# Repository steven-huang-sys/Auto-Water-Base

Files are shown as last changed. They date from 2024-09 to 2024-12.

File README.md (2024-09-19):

# Senior Design Project Fall 2024
## Autonomous Watering System - Base Station
This repository contains the code for the microcontroller used in the base station of the system. Not everything is uploaded as the repository would be way too big with the build files. I used the ESP-IDF setup within VSCode.

## Specifications
### Microcontrollers
Tested on an ESP-WROOM-32
Intended to be an ESP32-S3 on the final product

### Display
2.2in TFT LCD Display with ILI9488 Drivers. SPI interface

## Schematic Notes
This is on KiCAD 6.0. Footprints for the ESP32 can be found here: https://github.com/espressif/kicad-libraries/tree/legacy_kicad6?tab=readme-ov-file

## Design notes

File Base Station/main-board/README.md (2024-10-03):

# Main Board of the Base Station
This contains the code and build for the ESP32 planned to be inside the hub.

## Self Notes
- Remember to run the menuconfig as Bluetooth needs to be enabled before the code can be built. Adding an sdkconfig.default would also work.
- Currently using NimBLE instead of Bluedroid stack as we likely don't need Bluetooth Classic.

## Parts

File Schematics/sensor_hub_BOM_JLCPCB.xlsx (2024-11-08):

Comment | Designator | Footprint | JLCPCB Part#(optional)
1u | C1, C6, C18 | Capacitor_SMD:C_0805_2012Metric_Pad1.18x1.45mm_HandSolder | C116352
4.7u | C2 | Capacitor_SMD:C_0805_2012Metric_Pad1.18x1.45mm_HandSolder | C1779
10u | C3, C19 | Capacitor_SMD:C_0805_2012Metric_Pad1.18x1.45mm_HandSolder | C15850
0.1u | C4, C5, C8, C9, C12 | Capacitor_SMD:C_0805_2012Metric_Pad1.18x1.45mm_HandSolder | C1711
15p | C7, C10 | Capacitor_SMD:C_0805_2012Metric_Pad1.18x1.45mm_HandSolder | C63339
22u | C11 | Capacitor_SMD:C_0805_2012Metric_Pad1.18x1.45mm_HandSolder | C45783
1n | C13, C14, C15, C16, C17 | Capacitor_SMD:C_0805_2012Metric_Pad1.18x1.45mm_HandSolder | C46653
ESD9B5.0ST5G | D1, D2, D8 | Diode_SMD:D_SOD-923 | C111566
LED | D3, D4, D6, D7 | LED_SMD:LED_0805_2012Metric_Pad1.15x1.40mm_HandSolder | C2297
40V | D5 | Diode_SMD:D_SOD-123F | C779674
120 ohms | FB1 | Resistor_SMD:R_0805_2012Metric_Pad1.20x1.40mm_HandSolder | C79382
MountingHole | H1, H2, H3, H4, H5, H6 | MountingHole:MountingHole_3.2mm_M3
USB_C_Receptacle_USB2.0 | J1 | Connector_USB:USB_C_Receptacle_HRO_TYPE-C-31-M-12 | C165948
Conn_01x03 | J2 | Connector_JST:JST_PH_B3B-PH-K_1x03_P2.00mm_Vertical | C131339
Conn_01x09_Male | J3 | Connector_PinHeader_2.54mm:PinHeader_1x09_P2.54mm_Vertical | C22438292
BC818 | Q1, Q2 | Package_TO_SOT_SMD:SOT-23 | C154797
4.12k | R1 | Resistor_SMD:R_0805_2012Metric_Pad1.20x1.40mm_HandSolder | C218607
1.18k | R2 | Resistor_SMD:R_0805_2012Metric_Pad1.20x1.40mm_HandSolder | C2077400
1.13k | R3 | Resistor_SMD:R_0805_2012Metric_Pad1.20x1.40mm_HandSolder | C322246
5.1k | R4, R5 | Resistor_SMD:R_0805_2012Metric_Pad1.20x1.40mm_HandSolder | C26023
1.5k | R6, R7, R8 | Resistor_SMD:R_0805_2012Metric_Pad1.20x1.40mm_HandSolder | C126687
300 | R9 | Resistor_SMD:R_0805_2012Metric_Pad1.20x1.40mm_HandSolder | C2828726
R | R10, R13 | Resistor_SMD:R_0805_2012Metric_Pad1.20x1.40mm_HandSolder | C25275
Optional | R11 | Resistor_SMD:R_0805_2012Metric_Pad1.20x1.40mm_HandSolder
10k | R12, R15, R16, R17, R18, R19, R20, R21, R22, R23, R24, R28, R31, R32 | Resistor_SMD:R_0805_2012Metric_Pad1.20x1.40mm_HandSolder | C17414
0 | R14, R29, R30, R33, R34 | Resistor_SMD:R_0805_2012Metric_Pad1.20x1.40mm_HandSolder | C25275
22.1k | R25 | Resistor_SMD:R_0805_2012Metric_Pad1.20x1.40mm_HandSolder | C17552
47.5k | R26 | Resistor_SMD:R_0805_2012Metric_Pad1.20x1.40mm_HandSolder | C26011
1k | R27 | Resistor_SMD:R_0805_2012Metric_Pad1.20x1.40mm_HandSolder | C25623
SW_Push | SW1, SW2 | JLCPCB_Components:Switch_Small | C967766
SW_Push | SW3, SW4, SW5, SW6, SW7 | Button_Switch_THT:SW_PUSH-12mm
BQ24074RGT | U1 | Package_DFN_QFN:VQFN-16-1EP_3x3mm_P0.5mm_EP1.6x1.6mm | C54313
LD1117S33TR_SOT223 | U2 | Package_TO_SOT_SMD:SOT-223-3_TabPin2 | C86781
ESP32-S3-WROOM-1 | U3 | Espressif:ESP32-S3-WROOM-1U | C3013946
CP2102N-Axx-xQFN28 | U4 | Package_DFN_QFN:QFN-28-1EP_5x5mm_P0.5mm_EP3.35x3.35mm | C964632
32.768 kHz | Y1 | Crystal:Crystal_SMD_3215-2Pin_3.2x1.5mm

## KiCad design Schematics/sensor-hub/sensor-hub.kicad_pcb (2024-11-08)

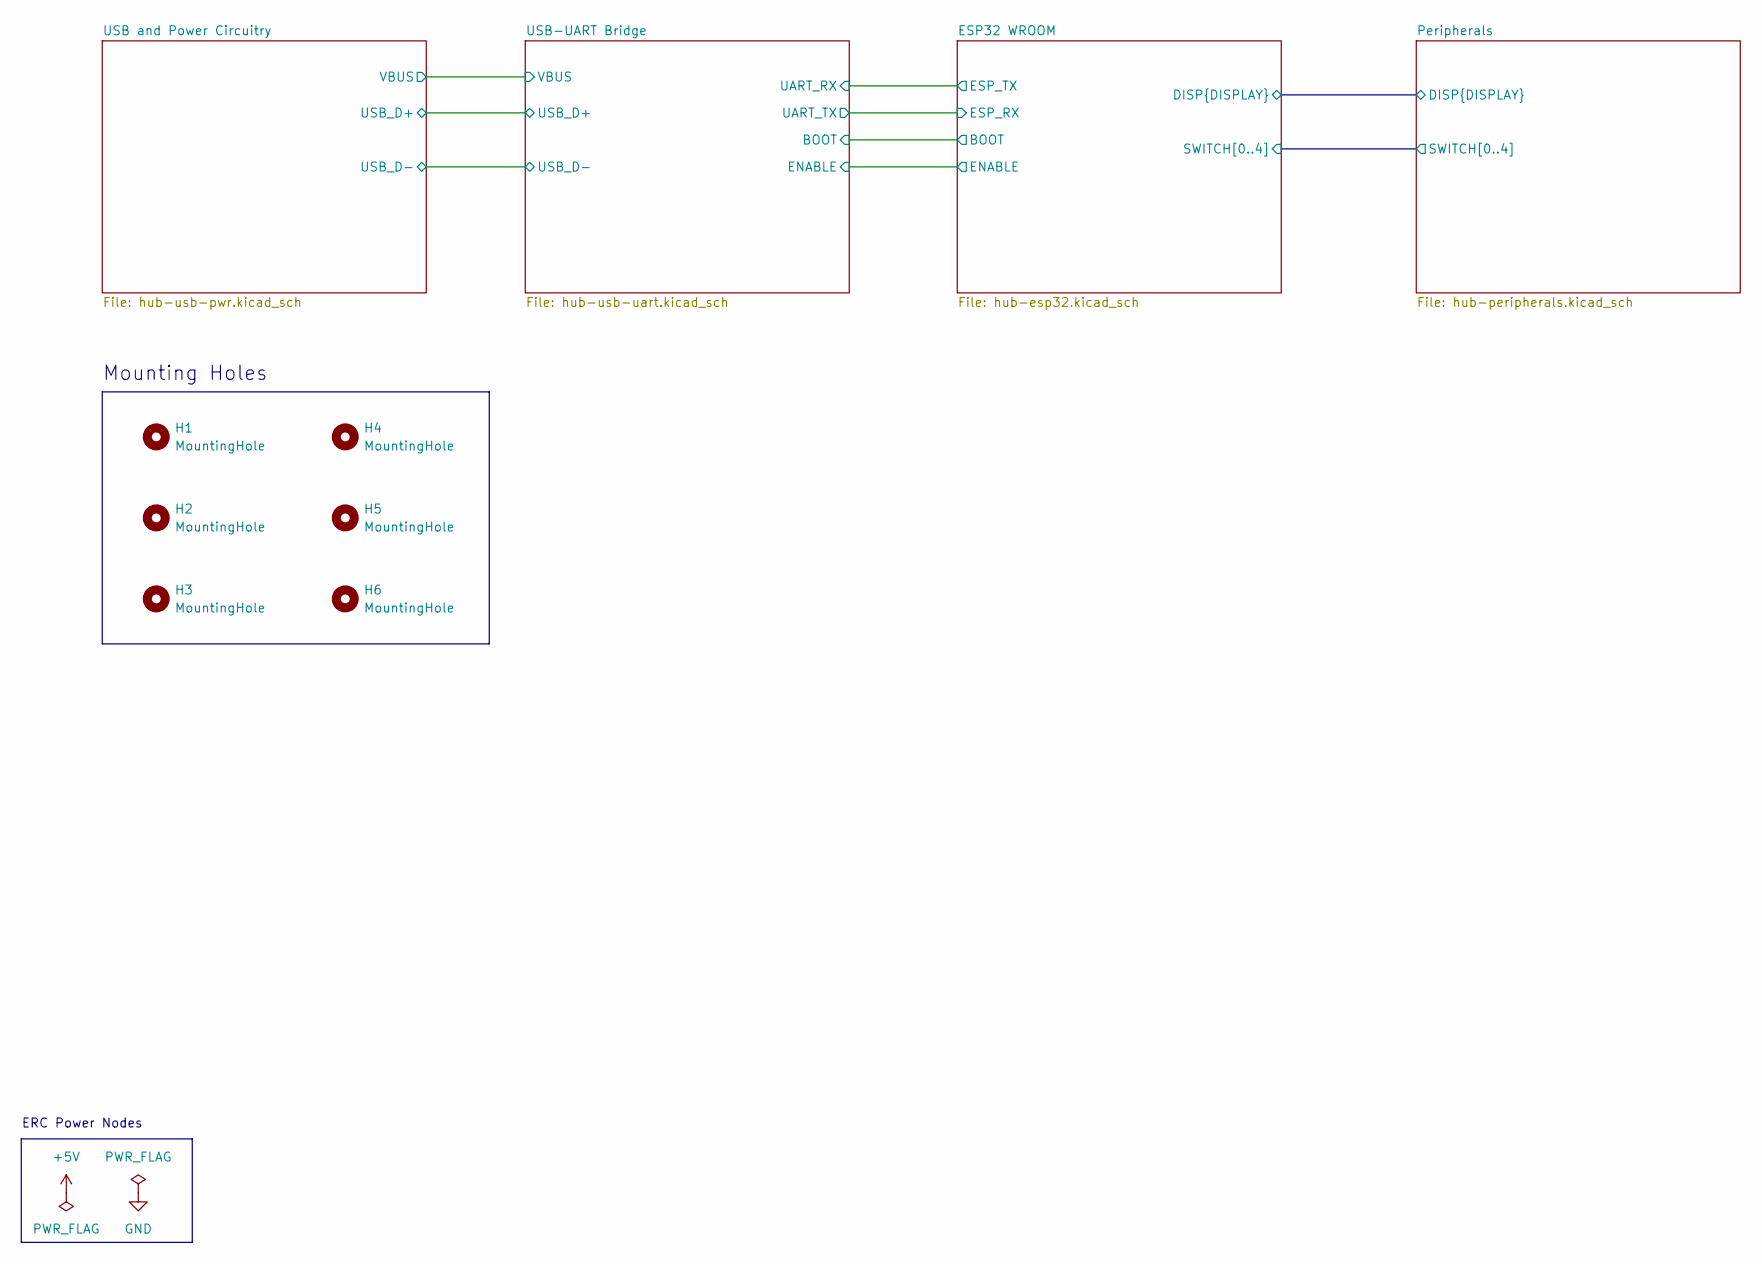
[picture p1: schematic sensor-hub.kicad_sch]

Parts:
H1, H2, H3, H4, H5, H6: MountingHole; MountingHole_3.2mm_M3

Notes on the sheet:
ERC Power Nodes
Mounting Holes

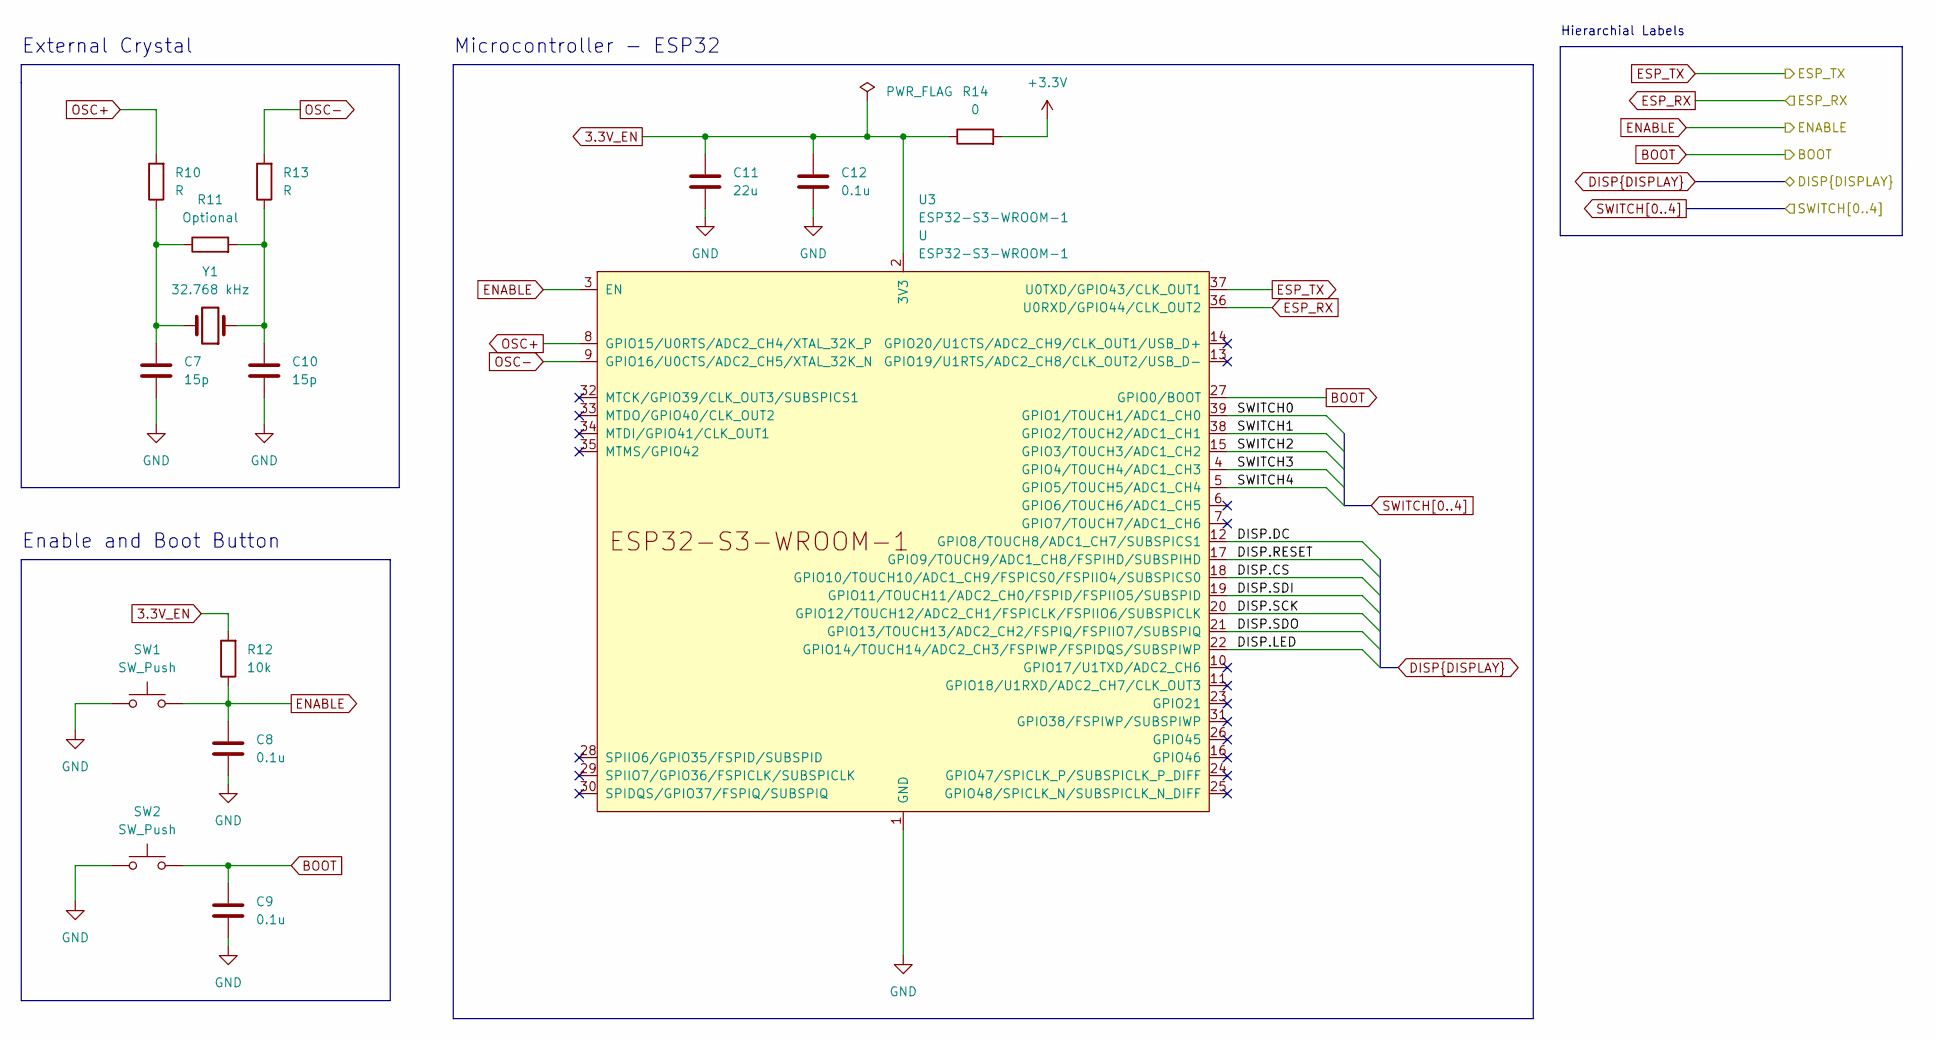
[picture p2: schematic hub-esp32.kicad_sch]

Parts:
C7, C10: 15p; C_0805_2012Metric_Pad1.18x1.45mm_HandSolder
C8, C9, C12: 0.1u; C_0805_2012Metric_Pad1.18x1.45mm_HandSolder
C11: 22u; C_0805_2012Metric_Pad1.18x1.45mm_HandSolder
R10, R13: R; R_0805_2012Metric_Pad1.20x1.40mm_HandSolder
R11: Optional; R_0805_2012Metric_Pad1.20x1.40mm_HandSolder
R12: 10k; R_0805_2012Metric_Pad1.20x1.40mm_HandSolder
R14: 0; R_0805_2012Metric_Pad1.20x1.40mm_HandSolder
SW1, SW2: SW_Push; Switch_Small
U3: ESP32-S3-WROOM-1; ESP32-S3-WROOM-1U
Y1: 32.768 kHz; Crystal_SMD_3215-2Pin_3.2x1.5mm

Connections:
3.3V_EN: C11.2, C12.2, R12.2, R14.1, U3.2 (3V3)
+3V3: R14.2; also elsewhere on the board
BOOT: C9.2, SW2.2, U3.27 (GPIO0/BOOT); also elsewhere on the board
DISP.CS: U3.18 (GPIO10/TOUCH10/ADC1_CH9/FSPICS0/FSPIIO4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); also elsewhere on the board
DISP.DC: U3.12 (GPIO8/TOUCH8/ADC1_CH7/SUBSPICS1); also elsewhere on the board
DISP.LED: U3.22 (GPIO14/TOUCH14/ADC2_CH3/FSPIWP/FSPIDQS/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); also elsewhere on the board
DISP.RESET: U3.17 (GPIO9/TOUCH9/ADC1_CH8/FSPIHD/SUBSPIHD); also elsewhere on the board
DISP.SCK: U3.20 (GPIO12/TOUCH12/ADC2_CH1/FSPICLK/FSPIIO6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); also elsewhere on the board
DISP.SDI: U3.19 (GPIO11/TOUCH11/ADC2_CH0/FSPID/FSPIIO5/S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); also elsewhere on the board
DISP.SDO: U3.21 (GPIO13/TOUCH13/ADC2_CH2/FSPIQ/FSPIIO7/S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); also elsewhere on the board
ENABLE: C8.2, R12.1, SW1.2, U3.3 (EN); also elsewhere on the board
ESP_RX: U3.36 (U0RXD/GPIO44/CLK_OUT2); also elsewhere on the board
GND: C7.2, C8.1, C9.1, C10.2, C11.1, C12.1, SW1.1, SW2.1, U3.1 (GND), U3.40 (GND), U3.41 (GND); also elsewhere on the board
unnamed: C7.1, R10.1, R11.1, Y1.2
unnamed: C10.1, R11.2, R13.1, Y1.1
OSC+: R10.2, U3.8 (GPIO15/U0RTS/ADC2_CH4/XTAL_32K_P)
OSC-: R13.2, U3.9 (GPIO16/U0CTS/ADC2_CH5/XTAL_32K_N)
SWITCH0: U3.39 (GPIO1/TOUCH1/ADC1_CH0); also elsewhere on the board
SWITCH1: U3.38 (GPIO2/TOUCH2/ADC1_CH1); also elsewhere on the board
SWITCH2: U3.15 (GPIO3/TOUCH3/ADC1_CH2); also elsewhere on the board
SWITCH3: U3.4 (GPIO4/TOUCH4/ADC1_CH3); also elsewhere on the board
SWITCH4: U3.5 (GPIO5/TOUCH5/ADC1_CH4); also elsewhere on the board
UART_RX: U3.37 (U0TXD/GPIO43/CLK_OUT1); also elsewhere on the board

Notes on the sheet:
External Crystal
Enable and Boot Button
Hierarchial Labels
Microcontroller - ESP32

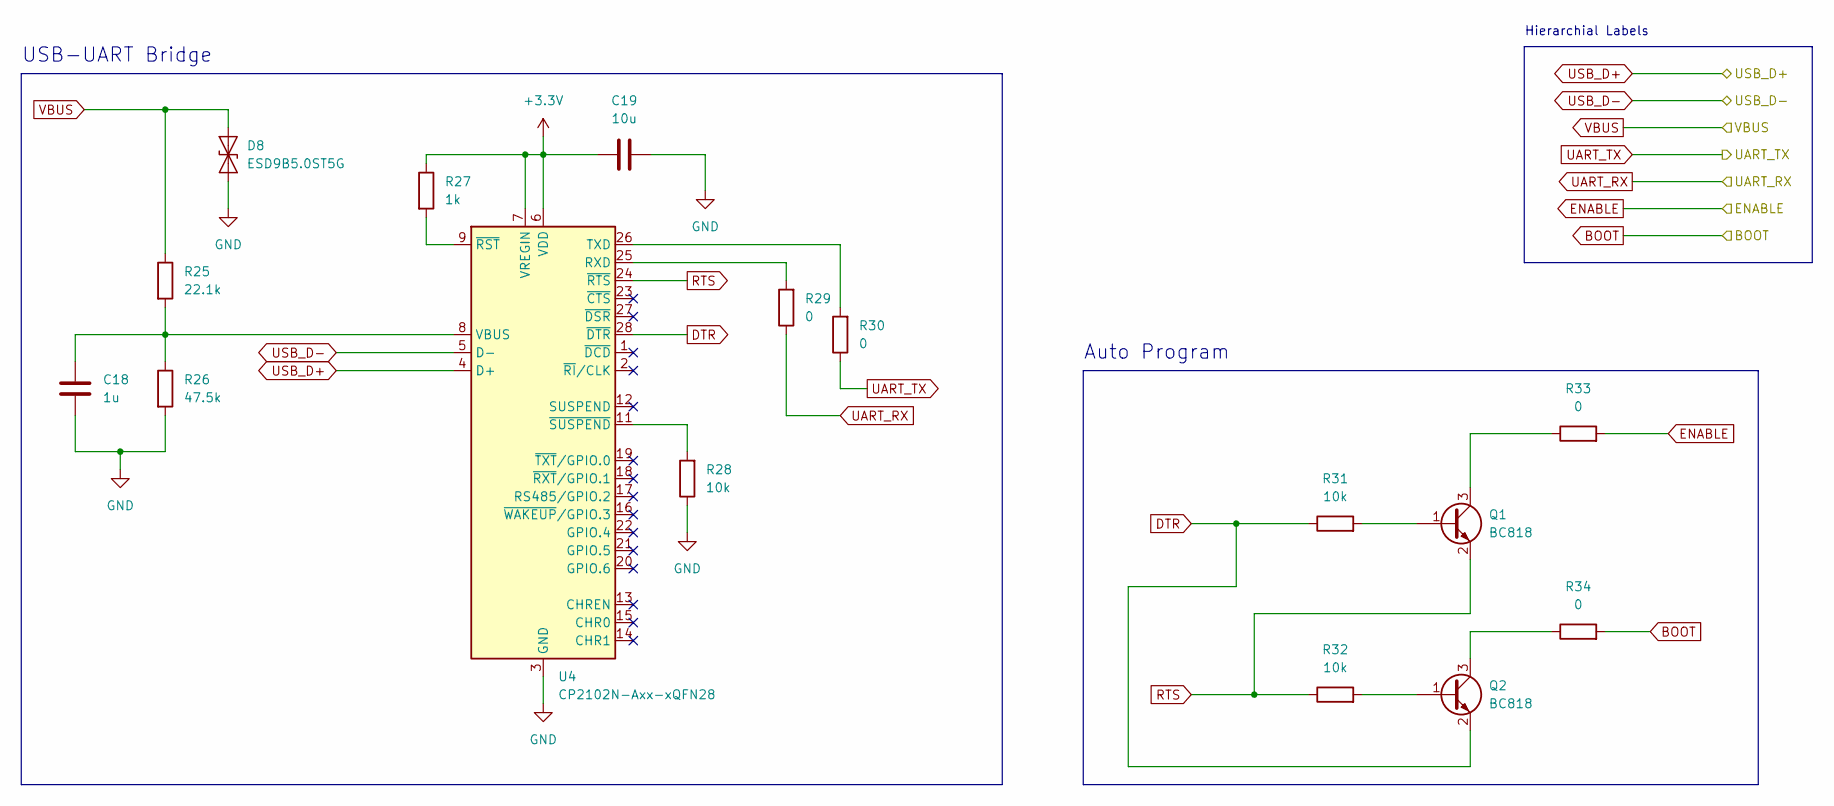
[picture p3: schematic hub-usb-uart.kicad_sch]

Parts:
C18: 1u; C_0805_2012Metric_Pad1.18x1.45mm_HandSolder
C19: 10u; C_0805_2012Metric_Pad1.18x1.45mm_HandSolder
D8: ESD9B5.0ST5G; D_SOD-923
Q1, Q2: BC818; SOT-23
R25: 22.1k; R_0805_2012Metric_Pad1.20x1.40mm_HandSolder
R26: 47.5k; R_0805_2012Metric_Pad1.20x1.40mm_HandSolder
R27: 1k; R_0805_2012Metric_Pad1.20x1.40mm_HandSolder
R28, R31, R32: 10k; R_0805_2012Metric_Pad1.20x1.40mm_HandSolder
R29, R30, R33, R34: 0; R_0805_2012Metric_Pad1.20x1.40mm_HandSolder
U4: CP2102N-Axx-xQFN28; QFN-28-1EP_5x5mm_P0.5mm_EP3.35x3.35mm

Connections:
+3V3: C19.1, R27.1, U4.6 (VDD), U4.7 (VREGIN); also elsewhere on the board
BOOT: R34.2; also elsewhere on the board
DTR: Q2.2 (E), R31.1, U4.28 (~DTR)
ENABLE: R33.2; also elsewhere on the board
ESP_RX: R30.1; also elsewhere on the board
GND: C18.1, C19.2, D8.2 (A2), R26.2, R28.1, U4.3 (GND), U4.29 (GND); also elsewhere on the board
unnamed: C18.2, R25.2, R26.1, U4.8 (VBUS)
unnamed: Q1.1 (B), R31.2
unnamed: Q1.3 (C), R33.1
unnamed: Q2.1 (B), R32.2
unnamed: Q2.3 (C), R34.1
unnamed: R27.2, U4.9 (~RST)
unnamed: R28.2, U4.11 (~SUSPEND)
unnamed: R29.2, U4.25 (RXD)
unnamed: R30.2, U4.26 (TXD)
RTS: Q1.2 (E), R32.1, U4.24 (~RTS)
UART_RX: R29.1; also elsewhere on the board
USB_D+: U4.4 (D+); also elsewhere on the board
USB_D-: U4.5 (D-); also elsewhere on the board
VBUS: D8.1 (A1), R25.1; also elsewhere on the board

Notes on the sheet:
Auto Program
Hierarchial Labels
USB-UART Bridge

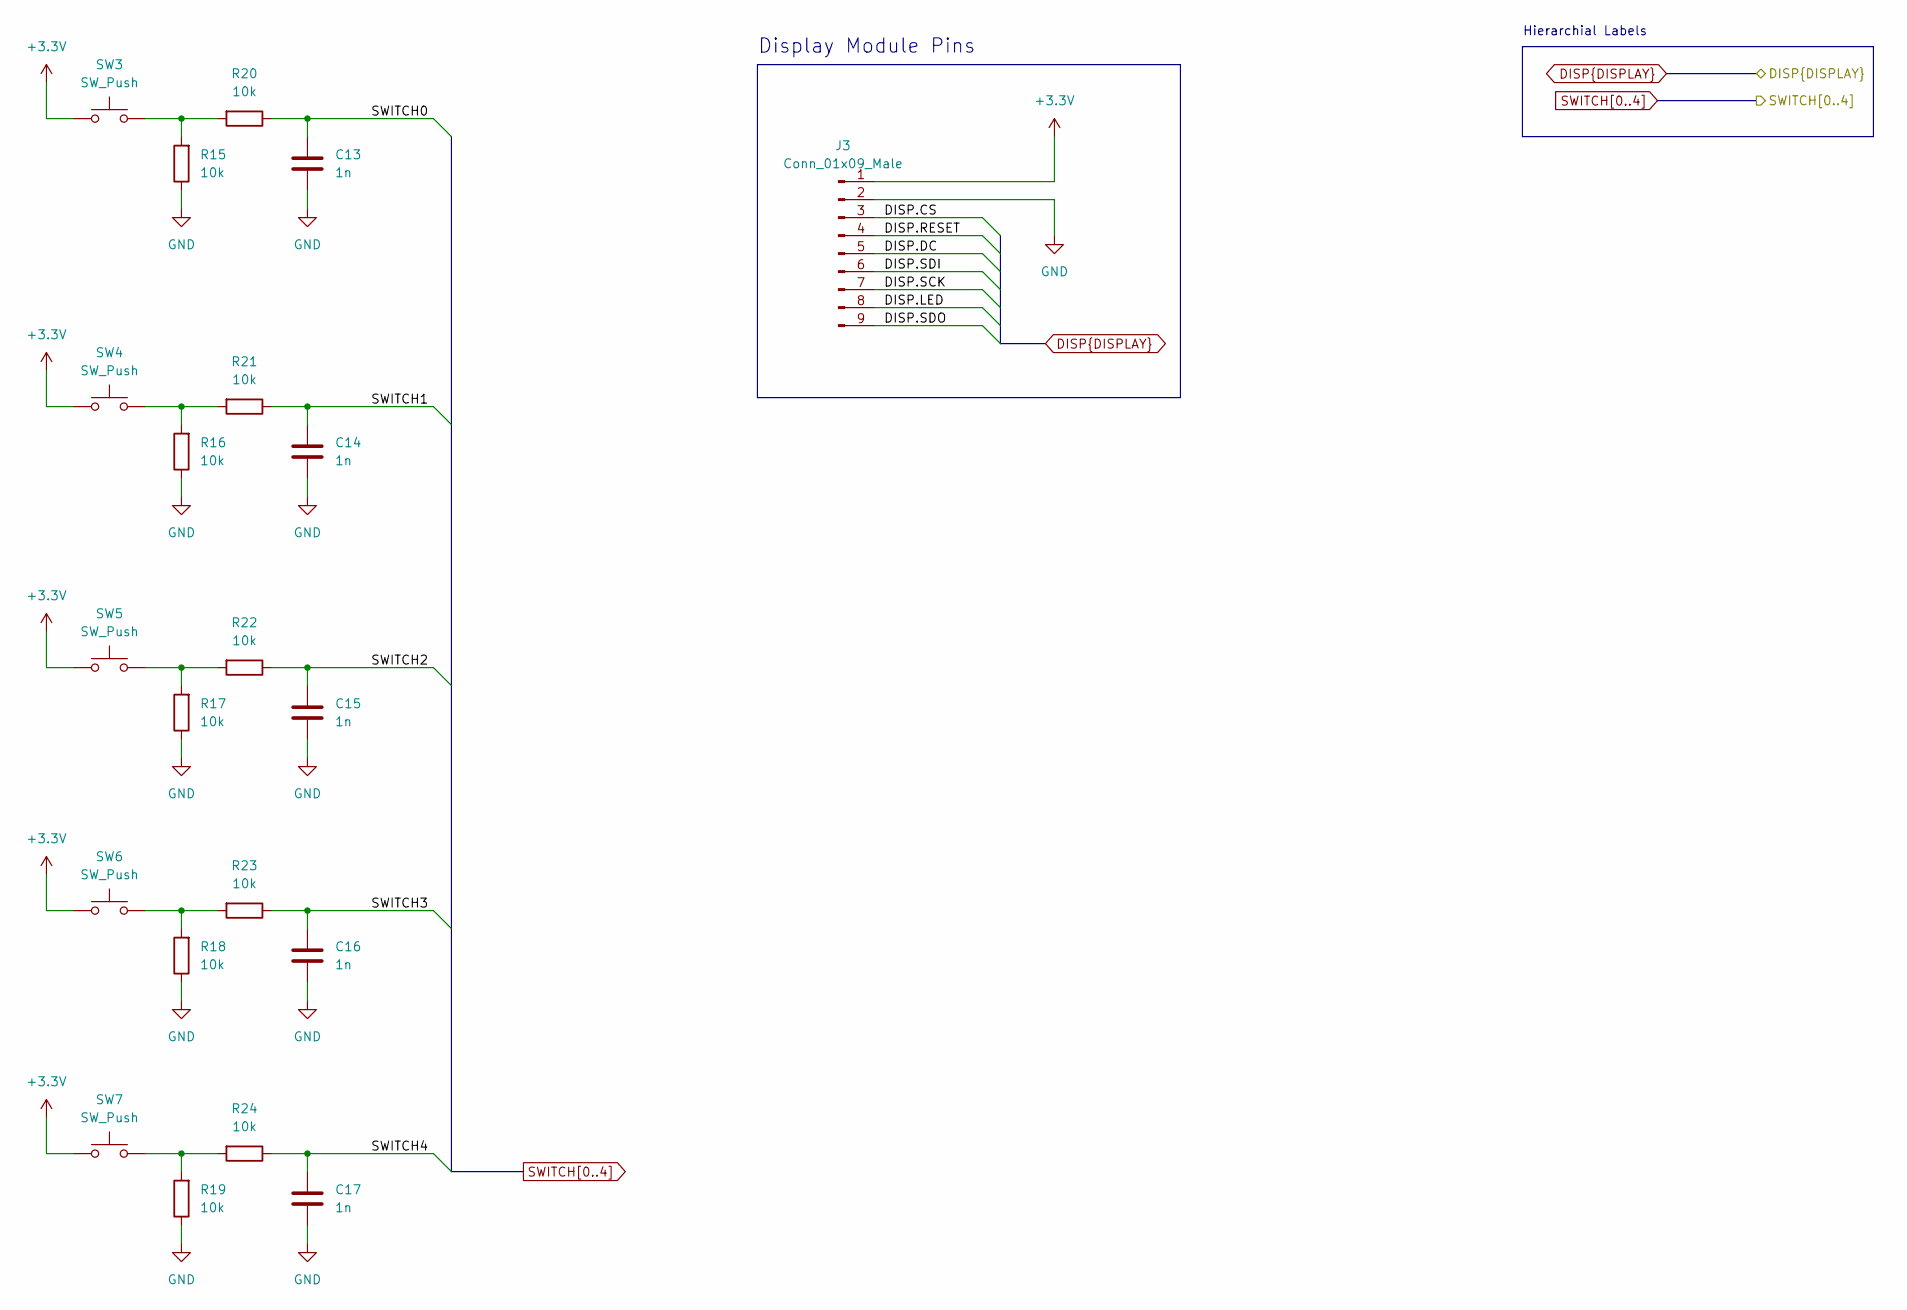
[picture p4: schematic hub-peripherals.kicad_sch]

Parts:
C13, C14, C15, C16, C17: 1n; C_0805_2012Metric_Pad1.18x1.45mm_HandSolder
J3: Conn_01x09_Male; PinHeader_1x09_P2.54mm_Vertical
R15, R16, R17, R18, R19, R20, R21, R22, R23, R24: 10k; R_0805_2012Metric_Pad1.20x1.40mm_HandSolder
SW3, SW4, SW5, SW6, SW7: SW_Push; SW_PUSH-12mm

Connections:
+3V3: J3.1, SW3.1, SW4.1, SW5.1, SW6.1, SW7.1; also elsewhere on the board
DISP.CS: J3.3; also elsewhere on the board
DISP.DC: J3.5; also elsewhere on the board
DISP.LED: J3.8; also elsewhere on the board
DISP.RESET: J3.4; also elsewhere on the board
DISP.SCK: J3.7; also elsewhere on the board
DISP.SDI: J3.6; also elsewhere on the board
DISP.SDO: J3.9; also elsewhere on the board
GND: C13.1, C14.1, C15.1, C16.1, C17.1, J3.2, R15.1, R16.1, R17.1, R18.1, R19.1; also elsewhere on the board
unnamed: R15.2, R20.2, SW3.2
unnamed: R16.2, R21.2, SW4.2
unnamed: R17.2, R22.2, SW5.2
unnamed: R18.2, R23.2, SW6.2
unnamed: R19.2, R24.2, SW7.2
SWITCH0: C13.2, R20.1; also elsewhere on the board
SWITCH1: C14.2, R21.1; also elsewhere on the board
SWITCH2: C15.2, R22.1; also elsewhere on the board
SWITCH3: C16.2, R23.1; also elsewhere on the board
SWITCH4: C17.2, R24.1; also elsewhere on the board

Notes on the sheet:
Display Module Pins
Hierarchial Labels

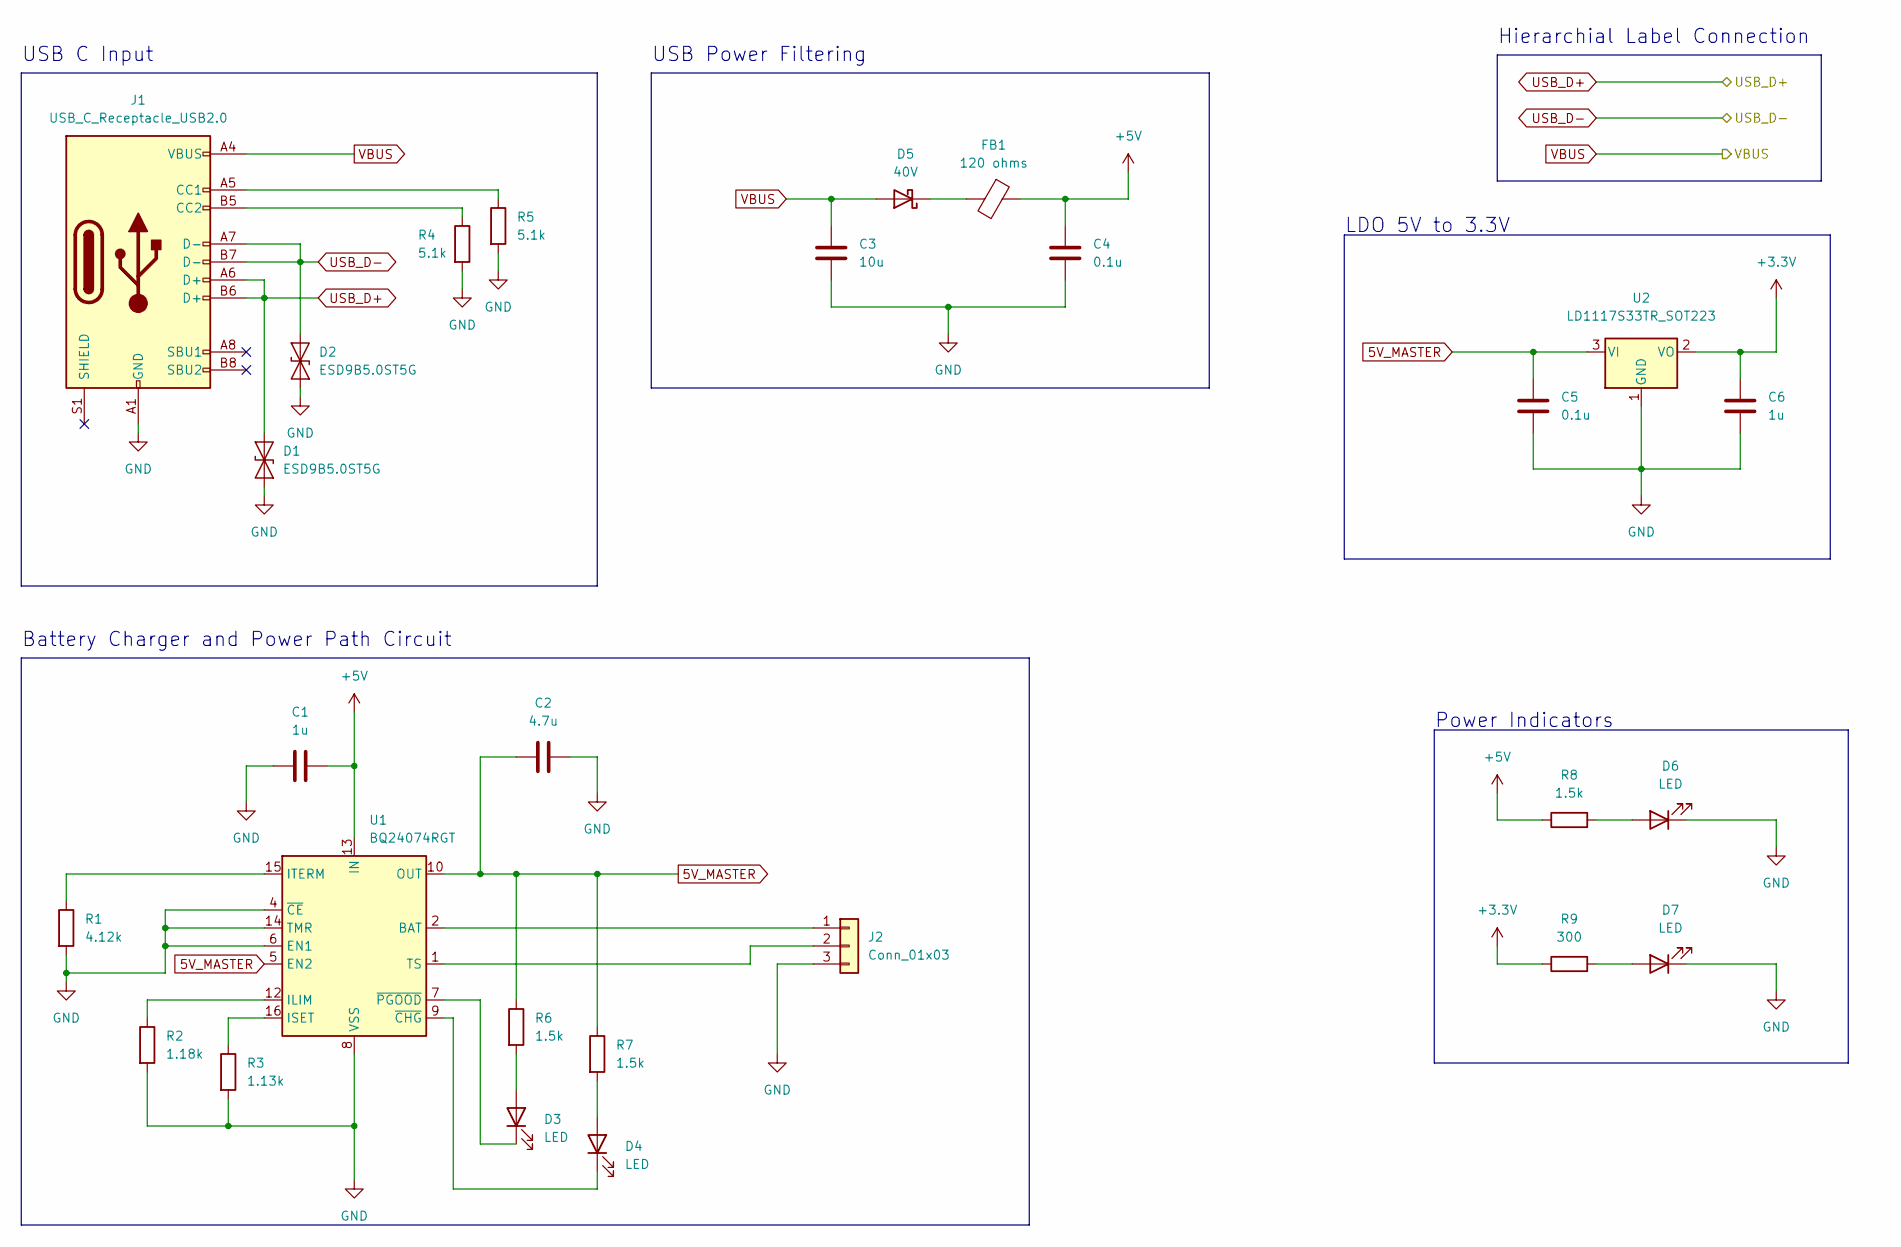
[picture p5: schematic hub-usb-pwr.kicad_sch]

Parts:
C1, C6: 1u; C_0805_2012Metric_Pad1.18x1.45mm_HandSolder
C2: 4.7u; C_0805_2012Metric_Pad1.18x1.45mm_HandSolder
C3: 10u; C_0805_2012Metric_Pad1.18x1.45mm_HandSolder
C4, C5: 0.1u; C_0805_2012Metric_Pad1.18x1.45mm_HandSolder
D1, D2: ESD9B5.0ST5G; D_SOD-923
D3, D4, D6, D7: LED; LED_0805_2012Metric_Pad1.15x1.40mm_HandSolder
D5: 40V; D_SOD-123F
FB1: 120 ohms; R_0805_2012Metric_Pad1.20x1.40mm_HandSolder
J1: USB_C_Receptacle_USB2.0; USB_C_Receptacle_HRO_TYPE-C-31-M-12
J2: Conn_01x03; JST_PH_B3B-PH-K_1x03_P2.00mm_Vertical
R1: 4.12k; R_0805_2012Metric_Pad1.20x1.40mm_HandSolder
R2: 1.18k; R_0805_2012Metric_Pad1.20x1.40mm_HandSolder
R3: 1.13k; R_0805_2012Metric_Pad1.20x1.40mm_HandSolder
R4, R5: 5.1k; R_0805_2012Metric_Pad1.20x1.40mm_HandSolder
R6, R7, R8: 1.5k; R_0805_2012Metric_Pad1.20x1.40mm_HandSolder
R9: 300; R_0805_2012Metric_Pad1.20x1.40mm_HandSolder
U1: BQ24074RGT; VQFN-16-1EP_3x3mm_P0.5mm_EP1.6x1.6mm
U2: LD1117S33TR_SOT223; SOT-223-3_TabPin2

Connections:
5V_MASTER: C2.1, C5.1, R6.1, R7.1, U1.5 (EN2), U1.10 (OUT), U1.11 (OUT), U2.3 (VI)
+3V3: C6.2, R9.1, U2.2 (VO); also elsewhere on the board
+5V: C1.2, C4.1, FB1.1, R8.1, U1.13 (IN)
GND: C1.1, C2.2, C3.2, C4.2, C5.2, C6.1, D1.2 (A2), D2.2 (A2), D6.1 (K), D7.1 (K), J1.A1 (GND), J1.A12 (GND), J1.B1 (GND), J1.B12 (GND), J2.3, R1.2, R2.2, R3.2, R4.2, R5.2, U1.4 (~CE), U1.6 (EN1), U1.8 (VSS), U1.14 (TMR), U1.17 (VSS), U2.1 (GND); also elsewhere on the board
unnamed: D3.1 (K), U1.7 (~PGOOD)
unnamed: D3.2 (A), R6.2
unnamed: D4.1 (K), U1.9 (~CHG)
unnamed: D4.2 (A), R7.2
unnamed: D5.1 (K), FB1.2
unnamed: D6.2 (A), R8.2
unnamed: D7.2 (A), R9.2
unnamed: J1.A5 (CC1), R5.1
unnamed: J1.B5 (CC2), R4.1
unnamed: J2.1, U1.2 (BAT), U1.3 (BAT)
unnamed: J2.2, U1.1 (TS)
unnamed: R1.1, U1.15 (ITERM)
unnamed: R2.1, U1.12 (ILIM)
unnamed: R3.1, U1.16 (ISET)
USB_D+: D1.1 (A1), J1.A6 (D+), J1.B6 (D+); also elsewhere on the board
USB_D-: D2.1 (A1), J1.A7 (D-), J1.B7 (D-); also elsewhere on the board
VBUS: C3.1, D5.2 (A), J1.A4 (VBUS), J1.A9 (VBUS), J1.B4 (VBUS), J1.B9 (VBUS); also elsewhere on the board

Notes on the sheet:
Hierarchial Label Connection
LDO 5V to 3.3V
Power Indicators
USB Power Filtering
USB C Input
Battery Charger and Power Path Circuit

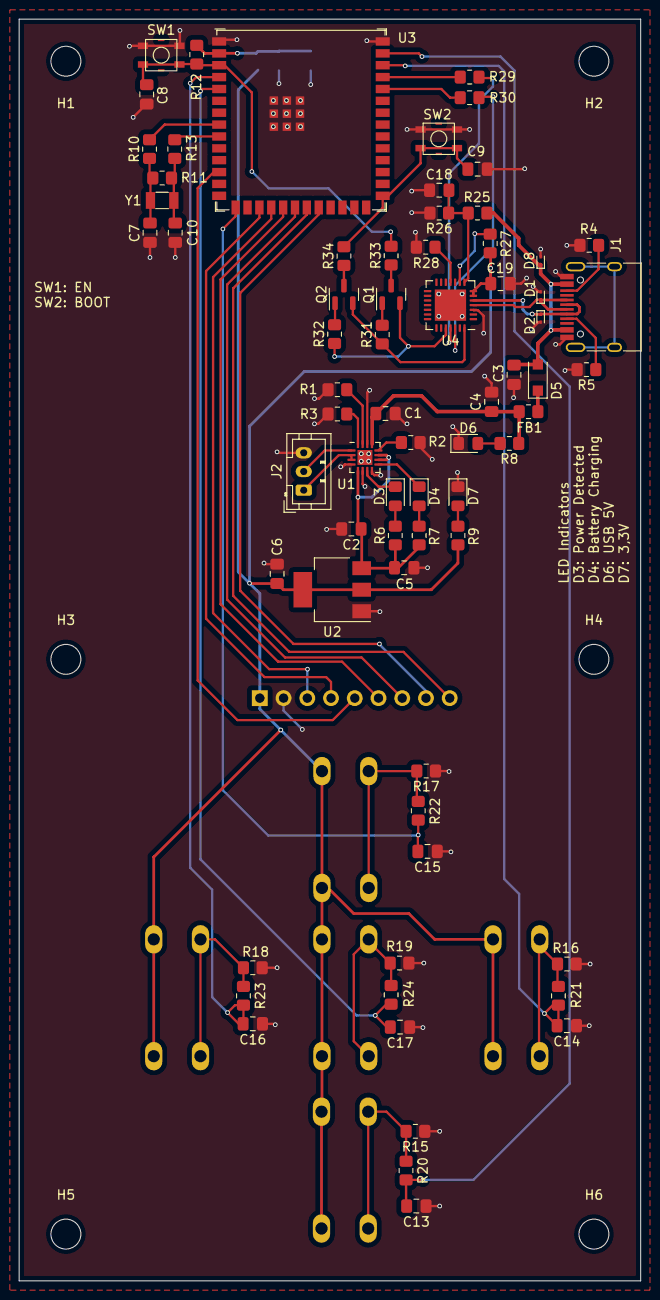
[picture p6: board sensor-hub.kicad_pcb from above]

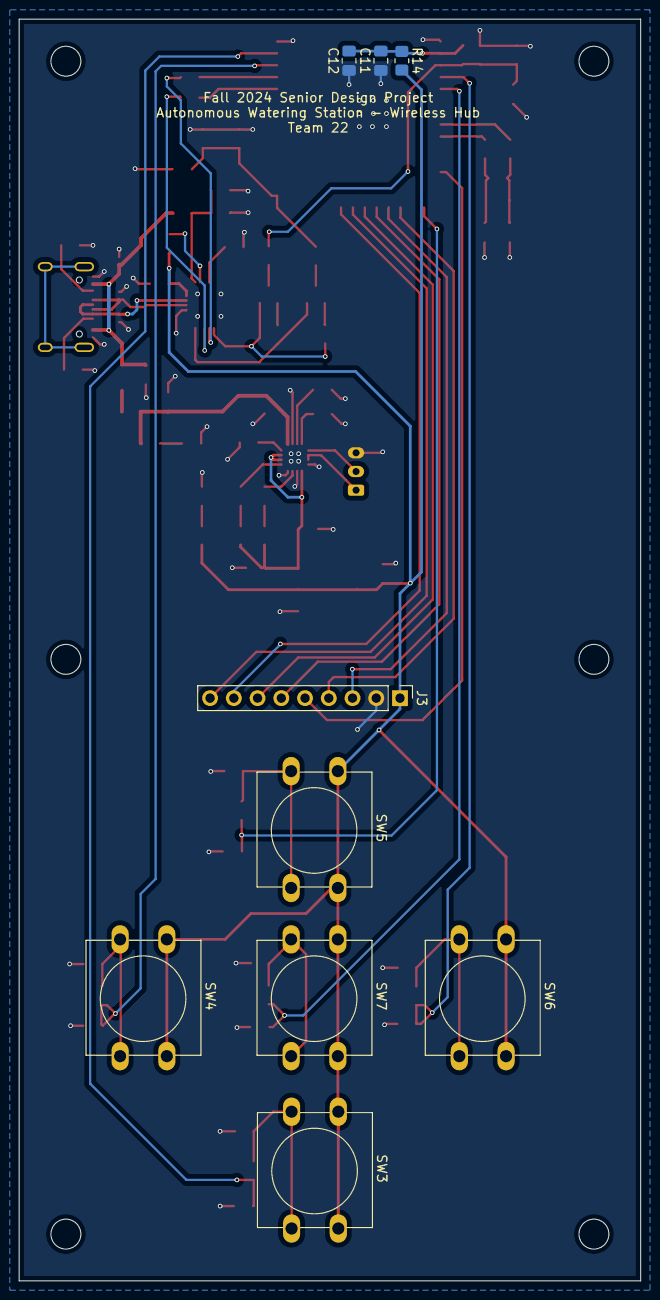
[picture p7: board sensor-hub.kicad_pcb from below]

Board: 2 copper layers, 66.5 x 135.0 mm, 85 parts (9 on the bottom side), 58 nets.

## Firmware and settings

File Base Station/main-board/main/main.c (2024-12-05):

#include <stdio.h>
#include <stdlib.h>
#include <string.h>
#include <inttypes.h>
#include "freertos/FreeRTOS.h"
#include "freertos/task.h"
#include "freertos/event_groups.h"
#include "esp_system.h"
#include "esp_log.h"
#include "nvs_flash.h"
#include "esp_event.h"

/* Bluetooth LE Module, make sure BT is enabled */
#include "ble_host.h"

/* WiFi Module */
#include "wifi_base.h"

/* Display Module */
#include "spi_display.h"

/* Buttons or Control Pad Module*/
#include "hub_controller.h"

/* Internet Clients */
#include "udp_client.h"
#include "http_client.h"

void app_main(void)
{
    
    control_init();

    esp_err_t esp_status;

    esp_status = nvs_flash_init();
    if (esp_status == ESP_ERR_NVS_NO_FREE_PAGES || esp_status == ESP_ERR_NVS_NEW_VERSION_FOUND) {
        ESP_ERROR_CHECK(nvs_flash_erase());
        esp_status = nvs_flash_init();
    }
    ESP_ERROR_CHECK(esp_status);

    // display_init();
    ble_init();
    wifi_init();
    // http_client_init();
    udp_client_init();

}

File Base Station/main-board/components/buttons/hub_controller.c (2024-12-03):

/* GPIO Example

   This example code is in the Public Domain (or CC0 licensed, at your option.)

   Unless required by applicable law or agreed to in writing, this
   software is distributed on an "AS IS" BASIS, WITHOUT WARRANTIES OR
   CONDITIONS OF ANY KIND, either express or implied.
*/
#include <stdio.h>
#include <string.h>
#include <stdlib.h>
#include <inttypes.h>
#include "freertos/FreeRTOS.h"
#include "freertos/task.h"
#include "freertos/queue.h"
#include "driver/gpio.h"
#include "hub_controller.h"
#include "esp_timer.h"
#include "shared_variables.h"

#define GPIO_INPUT_IO_0     1
#define GPIO_INPUT_IO_1     2
#define GPIO_INPUT_IO_2     3
#define GPIO_INPUT_IO_3     4
#define GPIO_INPUT_IO_4     5
#define GPIO_INPUT_PIN_SEL  ((1ULL<<GPIO_INPUT_IO_0) | (1ULL<<GPIO_INPUT_IO_1) | (1ULL<<GPIO_INPUT_IO_2) | (1ULL<<GPIO_INPUT_IO_3) | (1ULL<<GPIO_INPUT_IO_4))
/*
 * Let's say, GPIO_INPUT_IO_0=4, GPIO_INPUT_IO_1=5
 * In binary representation,
 * 1ULL<<GPIO_INPUT_IO_0 is equal to 0000000000000000000000000000000000010000 and
 * 1ULL<<GPIO_INPUT_IO_1 is equal to 0000000000000000000000000000000000100000
 * GPIO_INPUT_PIN_SEL                0000000000000000000000000000000000110000
 * */
#define ESP_INTR_FLAG_DEFAULT 0


// timer config

esp_timer_handle_t timer_handler;

static void timer_callback(void *param) {
    // delete timer
    esp_timer_delete(timer_handler);
    timer_handler = NULL;
}

const esp_timer_create_args_t timer_config = {
    .callback = &timer_callback,
    .name = "Timer"
};

// gpio handlers
static QueueHandle_t gpio_evt_queue = NULL;

static void IRAM_ATTR gpio_isr_handler(void* arg)
{
    if (timer_handler != NULL) {
        return;
    }
    ESP_ERROR_CHECK(esp_timer_create(&timer_config, &timer_handler));
    ESP_ERROR_CHECK(esp_timer_start_once(timer_handler, 200000));
    uint32_t gpio_num = (uint32_t) arg;
    xQueueSendFromISR(gpio_evt_queue, &gpio_num, NULL);
}

static void gpio_task_example(void* arg)
{
    uint32_t io_num;
    for (;;) {
        if (xQueueReceive(gpio_evt_queue, &io_num, portMAX_DELAY)) {
            printf("GPIO[%"PRIu32"] intr, val: %d\n", io_num, gpio_get_level(io_num));
            // io_num = 0;
        }  
    }
}

/*
static void gpio_polling(void* arg)
{
    for (;;) {
        if (gpio_get_level(GPIO_INPUT_IO_0)) {
            printf("GPIO[%d] pressed\n", GPIO_INPUT_IO_0);
        }
        else if (gpio_get_level(GPIO_INPUT_IO_1)) {
            printf("GPIO[%d] pressed\n", GPIO_INPUT_IO_1);
        }
        else if (gpio_get_level(GPIO_INPUT_IO_2)) {
            printf("GPIO[%d] pressed\n", GPIO_INPUT_IO_2);
        }
        else if (gpio_get_level(GPIO_INPUT_IO_3)) {
            printf("GPIO[%d] pressed\n", GPIO_INPUT_IO_3);
        }
        else if (gpio_get_level(GPIO_INPUT_IO_4)) {
            printf("GPIO[%d] pressed\n", GPIO_INPUT_IO_4);
        }
        vTaskDelay(200 / portTICK_PERIOD_MS);
    }
}
*/

void control_init(void)
{
    //zero-initialize the config structure.
    gpio_config_t io_conf = {};

    printf("Input config\n");
    //interrupt edge type
    io_conf.intr_type = GPIO_INTR_POSEDGE;
    //bit mask of the pins
    io_conf.pin_bit_mask = GPIO_INPUT_PIN_SEL;
    //set as input mode
    io_conf.mode = GPIO_MODE_INPUT;
    //pull-down mode
    io_conf.pull_down_en = 1;
    //pull-up mode
    io_conf.pull_up_en = 0;
    gpio_config(&io_conf);


    //change gpio interrupt type for one pin
    // gpio_set_intr_type(GPIO_INPUT_IO_0, GPIO_INTR_ANYEDGE);
    printf("Handler initialization\n");
    //create a queue to handle gpio event from isr
    gpio_evt_queue = xQueueCreate(10, sizeof(uint32_t));
    //start gpio task
    xTaskCreate(gpio_task_example, "gpio_task_example", 2048, NULL, 10, NULL);

    //install gpio isr service
    gpio_install_isr_service(ESP_INTR_FLAG_DEFAULT);
    //hook isr handler for specific gpio pin
    gpio_isr_handler_add(GPIO_INPUT_IO_0, gpio_isr_handler, (void*) GPIO_INPUT_IO_0);
    //hook isr handler for specific gpio pin
    gpio_isr_handler_add(GPIO_INPUT_IO_1, gpio_isr_handler, (void*) GPIO_INPUT_IO_1);
    gpio_isr_handler_add(GPIO_INPUT_IO_2, gpio_isr_handler, (void*) GPIO_INPUT_IO_2);
    gpio_isr_handler_add(GPIO_INPUT_IO_3, gpio_isr_handler, (void*) GPIO_INPUT_IO_3);
    gpio_isr_handler_add(GPIO_INPUT_IO_4, gpio_isr_handler, (void*) GPIO_INPUT_IO_4);
    

    // gpio polling
    // xTaskCreate(gpio_polling, "gpio_polling", 2048, NULL, 10, NULL);

    printf("Minimum free heap size: %"PRIu32" bytes\n", esp_get_minimum_free_heap_size());

}

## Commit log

2024-09-19 initial schematic files
    [sensor-hub.kicad_pcb, sensor-hub.kicad_sch]
2024-09-20 main board setup
2024-09-26 managers meeting schematics
    [hub-esp32.kicad_sch, hub-peripherals.kicad_sch, hub-usb-pwr.kicad_sch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]
2024-11-07 schematic and pcb upload
    [hub-esp32.kicad_sch, hub-peripherals.kicad_sch, hub-usb-pwr.kicad_sch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]
2024-11-07 removing ESP32 test and small updates
2024-11-08 updated BOM and pick and place
    [sensor_hub_BOM_JLCPCB.xlsx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]
2024-11-08 drill files added
    [sensor_hub_BOM_JLCPCB.xlsx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]
2024-11-08 evenly spaced out switches
    [sensor-hub-B_Cu.gbr, sensor-hub-B_Mask.gbr, sensor-hub-B_Paste.gbr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]
2024-12-03 this does not work
    [hub-peripherals.kicad_sch]
